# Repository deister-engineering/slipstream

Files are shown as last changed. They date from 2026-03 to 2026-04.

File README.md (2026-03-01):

# Slipstream

**This project is in beta. Please only attempt to build if you're an experienced builder and have a LOT of patience. Build instructions are not included.**

Slipstream is a high performance cross gantry/flying gantry 3D printer designed with scalability and speed in mind. It can be built as an open-air or fully enclosed printer, using a 2020 aluminum extrusion frame and MGN12H rails/carriages. The toolhead is based on the Annex K3, borrowing the MGN12H adaptation from @Etretti_376690 on Printables and modifying it to fit a Phaetus Rapido/Dragon hotend.

## Specifications
- Cross gantry cartesian kinematics
- Flying gantry (bed is static, gantry moves with Z axis)
- Quad-leveled gantry
- Enclosed or open air
- 2020 frame
- MGN12 rails/carriages
- Annex K3-based toolhead
- NEMA 17 motors for all axes of motion
- 9mm belts for XY motion, 6mm belts for Z
- 10:1 reduction pulley drive for Z axis

## Images

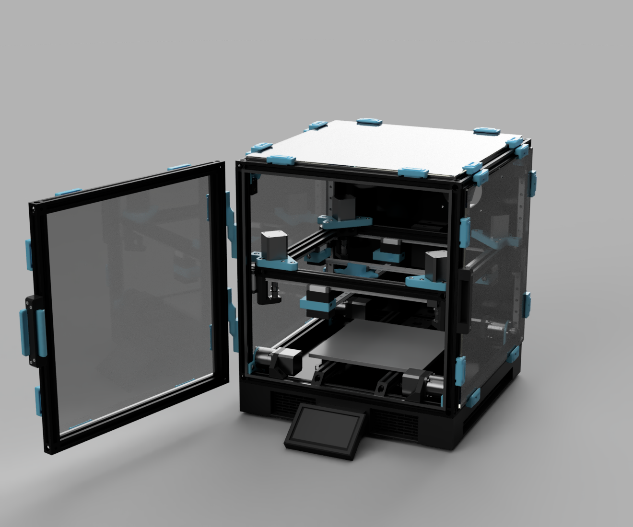
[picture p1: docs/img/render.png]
Image of Slipstream


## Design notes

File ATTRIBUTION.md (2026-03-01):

This project incorporates the following third-party works:

- MGN12H Rail + Carriage
  - by LiMo Bearing
  - Source: https://limobearing.com/3d-step-files
  - License can be found [here](https://limobearing.com/3d-step-files#:~:text=CAD%20File%20License%20Agreement)
  - Modifications: Rail chamfers removed for ease of positioning

- Fridge Door Lock Latch
  - by Inertia Bros
  - Source: https://github.com/Inertia-Bros/Inertia-Cube/tree/main/User-mods/2020%20Lock%20Latch%20-%20TheVoronModder
  - License: CC BY-NC-SA 4.0
  - Modifications: Removed logo, changed part colors, adjusted latch to clear thicker glass

- K3 MGN12 Toolhead
  - by @Etretti_376690
  - Source: https://www.printables.com/model/748199-k3-toolhead-carriage-mgn12
  - License: CC BY-NC 4.0
  - Modifications: Modified to fit Phaetus Rapido

- 5 inch DSI LCD
  - by Waveshare
  - Source: https://www.waveshare.com/wiki/5inch_DSI_LCD
  - License: No specific license, but was granted permission
  - No modifications

- Voron 2.4 Panel Locker
  - Copyright (c) 2024, v6cl
  - License: BSD 2-Clause
  - Source: https://github.com/v6cl/MyDIYthings/tree/main/3Dprinters/Utils/Panel_Locker
  - Modifications: spacing adjusted to support panel width, joints added to component for easier positioning + modeling. Changes are licensed under CC BY-NC-SA 4.0.
  - Panel Locker copyright notice: 
```
Voron 2.4 Panel Locker
BSD 2-Clause License

Copyright (c) 2024, v6cl

Redistribution and use in source and binary forms, with or without
modification, are permitted provided that the following conditions are met:

1. Redistributions of source code must retain the above copyright notice, this
   list of conditions and the following disclaimer.

2. Redistributions in binary form must reproduce the above copyright notice,
   this list of conditions and the following disclaimer in the documentation
   and/or other materials provided with the distribution.

THIS SOFTWARE IS PROVIDED BY THE COPYRIGHT HOLDERS AND CONTRIBUTORS "AS IS"
AND ANY EXPRESS OR IMPLIED WARRANTIES, INCLUDING, BUT NOT LIMITED TO, THE
IMPLIED WARRANTIES OF MERCHANTABILITY AND FITNESS FOR A PARTICULAR PURPOSE ARE
DISCLAIMED. IN NO EVENT SHALL THE COPYRIGHT HOLDER OR CONTRIBUTORS BE LIABLE
FOR ANY DIRECT, INDIRECT, INCIDENTAL, SPECIAL, EXEMPLARY, OR CONSEQUENTIAL
DAMAGES (INCLUDING, BUT NOT LIMITED TO, PROCUREMENT OF SUBSTITUTE GOODS OR
SERVICES; LOSS OF USE, DATA, OR PROFITS; OR BUSINESS INTERRUPTION) HOWEVER
CAUSED AND ON ANY THEORY OF LIABILITY, WHETHER IN CONTRACT, STRICT LIABILITY,
OR TORT (INCLUDING NEGLIGENCE OR OTHERWISE) ARISING IN ANY WAY OUT OF THE USE
OF THIS SOFTWARE, EVEN IF ADVISED OF THE POSSIBILITY OF SUCH DAMAGE.
```

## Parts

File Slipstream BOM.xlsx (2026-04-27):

Slipstream BOM - Beta | Fasteners are a rough minimum. Be prepared to purchase extras
 | Part Name | Number of items needed | Count of items per pack | Count to buy | Cost Each | Total Part Cost | Purchased? | Notes
Toolhead
 | GDSTIME 4020 Blower Fans (24V) (https://www.amazon.com/dp/B0DLKJ7WDJ) | 2 | 2 | 1 | $12.99 | $12.99 | FALSE
 | WINSINN 3010 Axial Fans (24V) (https://www.amazon.com/dp/B0757N6B8P) | 1 | 5 | 1 | $7.99 | $7.99 | FALSE
 | TZ-V6 2.0 (Choose any Dragon-compatible hotend) (https://www.amazon.com/Upgraded-Ceramic-Heatbreak-Hardened-Compatible/dp/B0CP64WYQW) | 1 | 1 | 1 | $28.99 | $28.99 | FALSE | Pretty sure this is a 2.0, so should be compatible with V6 nozzles
 | Fysetc CNC Sherpa Mini (https://www.amazon.com/FYSETC-Extruder-Temperature-Resistance-Compatible/dp/B0C3QGKQY6) | 1 | 1 | 1 | $85.66 | $85.66 | FALSE | There are more lightweight options
Glass
 | Acrylic Panels - SendCutSend Cart (https://cart.sendcutsend.com/7f6jah4ereyv) | 6 | 6 | 1 | $179.73 | $179.73 | FALSE | This cart is applicable if you're building a 220mm variant.
 | 5mm EVA foam tape (https://www.amazon.com/dp/B07L6LGMWC) | 8 | 4 | 2 | $7.19 | $14.38 | FALSE | Double this up - one strip on the frame side, one strip on the glass side. It will compress a bit
Frame
 | 2020 Extrusion - 400mm (https://www.amazon.com/dp/B0B2P434PD) | 16 | 10 | 2 | $36.99 | $73.98 | FALSE
 | 2020 Frame Block (https://www.amazon.com/dp/B0BG4TF813) | 16 | 8 | 2 | $16.89 | $33.78 | FALSE
 | 2020 90 Degree Frame Block 12x (https://www.amazon.com/dp/B0FRDJH8P2) | 4 | 12 | 1 | $18.39 | $18.39 | FALSE
Gantry
 | 2020 Extrusion - 350mm 4pcs (https://www.amazon.com/dp/B0B7DWDSYG) | 4 | 4 | 1 | $16.59 | $16.59 | FALSE
 | 2504 - 80mm shaft 48mm stepper (https://www.omc-stepperonline.com/nema-17-high-temp-stepper-motor-55ncm-77-93oz-in-80mm-5mm-d-cut-shaft-insulation-class-h-180c-17hs19-2504s-h-v5) | 4 | 1 | 4 | $15.00 | $60.00 | FALSE
 | MGN12H 350mm (https://www.amazon.com/CNCMANS-Miniature-Bearing-Printing-MGN12H-350mm/dp/B0BNQ99QWT) | 8 | 1 | 8 | $17.02 | $136.16 | FALSE
 | MGN12C 350mm (https://www.amazon.com/uxcell-Sliding-Carriage-Guideway-Engraving/dp/B0G5Y83MMT) | 2 | 1 | 2 | $19.99 | $39.98 | FALSE | These are for the cross rails. In the future, the outside rails of the gantry will likely move to MGN12C to cut down weight as well.
 | 625zz Bearing (https://www.amazon.com/uxcell-Groove-Bearings-Shielded-Bearing/dp/B0CJFRSK7D) | 8 | 25 | 1 | $7.79 | $7.79 | FALSE
 | GE5C Bearing (https://www.amazon.com/dp/B0CRNQYDFN) | 4 | 4 | 1 | $8.99 | $8.99 | FALSE
 | 9mm GT2 Timing Belt (10m) (https://www.amazon.com/dp/B0D7P815FL) | 1 | 1 | 1 | $25.99 | $25.99 | FALSE
 | 9mm GT2 Drive Pulley (https://www.amazon.com/dp/B0CNK9LKLV) | 4 | 10 | 1 | $12.98 | $12.98 | FALSE
 | 9mm GT2 Idler Pulley (https://www.amazon.com/dp/B0CNKBZFK8) | 4 | 10 | 1 | $13.98 | $13.98 | FALSE
 | 5mm to 5mm Shaft Coupling (https://www.amazon.com/dp/B0D4575J9B) | 4 | 10 | 1 | $8.49 | $8.49 | FALSE | Needed if going with steppers that don't have 80mm shafts. Recommend ~23mm shaft length from mounting face of stepper (OMC 17HS19-2004S1 are a good fit)
 | m5x8mmx0.5mm shims 100pk (https://www.amazon.com/dp/B0CF9H1R76) | 8 | 100 | 1 | $7.99 | $7.99 | FALSE
 | m5x8mmx1mm shims 50pk (https://www.fabreeko.com/products/m5-precision-brass-shims-m5x7x0-5?variant=45416233468159) | 8 | 100 | 1 | $6.99 | $6.99 | FALSE
Electronics
 | Meanwell LRS-350-48 (https://www.amazon.com/LRS-350-48-Switching-180-264VAC-Industrial-Efficient/dp/B0DJW8CMNJ) | 1 | 1 | 1 | $31.26 | $31.26 | FALSE
 | Meanwell LRS-350-24 (https://www.amazon.com/MEAN-WELL-LRS-350-24-350-4W-Switchable/dp/B013ETVO12) | 1 | 1 | 1 | $28.54 | $28.54 | FALSE
 | BTT Kraken (https://www.amazon.com/BIGTREETECH-Control-Onboard-8%C3%97TMC2160-Drivers/dp/B0F7RQY6Z4) | 1 | 1 | 1 | $129.99 | $129.99 | FALSE
 | Raspberry Pi 3B+ or newer (https://www.amazon.com/ELEMENT-Element14-Raspberry-Pi-Motherboard/dp/B07BDR5PDW) | 1 | 1 | 1 | $50.00 | $50.00 | FALSE
 | Fused IEC inlet (https://www.amazon.com/Qjaiune-IEC320-Socket-Rocker-Switch/dp/B09QFK6W2C) | 1 | 6 | 1 | $8.99 | $8.99 | FALSE
 | Cartographer V4 (https://cartographer3d.com/products/cartographer-v4-aio-standard) | 1 | 1 | 1 | $39.99 | $39.99 | FALSE
 | CAN wire (https://cartographer3d.com/products/microfit-3-0-can-cable-for-ebb36) | 1 | 1 | 1 | $15.00 | $15.00 | FALSE
Z axis
 | Creality 42-34 or comparable (14-18mm shaft length) (https://www.amazon.com/Creality-Official-42-34-3D-Compatible/dp/B09LQKWF7F) | 4 | 1 | 4 | $12.99 | $51.96 | FALSE
 | Stepperonline MG17-G10 Gearbox (https://www.omc-stepperonline.com/mg-series-planetary-gearbox-gear-ratio-10-1-backlash-30-arc-min-for-nema-17-stepper-motor-mg17-g10) | 4 | 1 | 4 | $15.60 | $62.40 | FALSE
 | GT2 20 tooth pulley/8mm bore/6mm belt (5 pack) (https://www.amazon.com/dp/B077GMKW1C) | 4 | 5 | 1 | $6.99 | $6.99 | FALSE
 | 15x15mm Cable Chain (https://www.amazon.com/dp/B07QYM88MQ) | 1 | 1 | 1 | $13.99 | $13.99 | FALSE
Bed
 | 235mm heated bed (any 4-point bed will do) (https://www.amazon.com/Aluminum-Heatbed-235%C3%97235x3mm-Ender-3-Printers/dp/B08DRJM9S4) | 1 | 1 | 1 | $22.99 | $22.99 | FALSE | Nicer option here. If you choose this, upgrade the 24v PSU to an LRS-350-24 or plan on getting an AC heater + a relay (https://www.amazon.com/dp/B0CMCDBJJF)
 | 235mm PEI build plate (https://www.amazon.com/235x235mm-Texture-Magnetic-Flexible-Creality/dp/B0CRDS6PRR) | 1 | 1 | 1 | $12.99 | $12.99 | FALSE
General
 | M2 heat inserts (https://www.amazon.com/dp/B0CTCQ6MHK) | 10 | 100 | 1 | $7.59 | $7.59 | FALSE | Only substitute exact dimensions. Count needed is approximate
 | M3 heat inserts 100ct (https://www.amazon.com/dp/B08TRK72TR) | 50 | 100 | 1 | $11.99 | $11.99 | FALSE | Only substitute exact dimensions. Count needed is approximate
 | M5 heat inserts 100ct (https://www.amazon.com/dp/B0F8HMZHTK) | 20 | 100 | 1 | $7.99 | $7.99 | FALSE | Only substitute exact dimensions. Count needed is approximate
 | Rubber Feet (https://www.amazon.com/Reliable-Hardware-Company-RH-1606-8-Amplifier/dp/B00JJ191Z6) | 4 | 8 | 1 | $9.99 | $9.99 | FALSE
 | Cable Chain (https://www.amazon.com/dp/B07QLGWQ1L) | 1 | 1 | 1 | $14.49 | $14.49 | FALSE
Fasteners | There are likely some fasteners missed in this list.
 | Hexagon Socket Button Head Screw ISO 7380-1 - M3 x 10 Steel 4.6 Plain |  | 16
 | Hexagon Socket Button Head Screw ISO 7380-1 - M3 x 16 Steel 4.6 Plain |  | 4
 | Hexagon Socket Button Head Screw ISO 7380-1 - M3 x 30 Steel 4.6 Plain |  | 8
 | Hexagon Socket Button Head Screw ISO 7380-1 - M3 x 55 Steel 4.6 Plain |  | 8
 | Hexagon Socket Button Head Screw ISO 7380-1 - M3 x 6 Steel 4.6 Plain |  | 8
 | Hexagon Socket Button Head Screw ISO 7380-1 - M3 x 8 Steel 4.6 Plain |  | 16
 | Hexagon Socket Button Head Screw ISO 7380-1 - M5 x 10 Steel 4.6 Plain |  | 12
 | Hexagon Socket Button Head Screw ISO 7380-1 - M5 x 12 Steel 4.6 Plain |  | 8
 | Hexagon Socket Button Head Screw ISO 7380-1 - M5 x 16 Steel 4.6 Plain |  | 56
 | Hexagon Socket Button Head Screw ISO 7380-1 - M5 x 20 Steel 4.6 Plain |  | 8
 | Hexagon Socket Button Head Screw ISO 7380-1 - M5 x 25 Steel 4.6 Plain |  | 2
 | Hexagon Socket Button Head Screw ISO 7380-1 - M5 x 30 Steel 4.6 Plain |  | 3
 | Hexagon Socket Button Head Screw ISO 7380-1 - M5 x 60 Steel 4.6 Plain |  | 4
 | Hexagon Socket Button Head Screw ISO 7380-1 - M5 x 75 Steel 4.6 Plain |  | 5
 | Hexagon Socket Button Head Screw ISO 7380-1 - M5 x 8 Steel 4.6 Plain |  | 28
 | Hexagon Socket Button Head Screw ISO 7380-1 - M5 x 90 Steel 4.6 Plain |  | 5
 | Hexagon Socket Head Cap Screw DIN 912 - M3 x 0.5 x 12 Steel 4.6 Plain |  | 6
 | Hexagon Socket Head Cap Screw DIN 912 - M3 x 0.5 x 16 Steel 4.6 Plain |  | 42
 | Hexagon Socket Head Cap Screw DIN 912 - M3 x 0.5 x 20 Steel 4.6 Plain |  | 24
 | Hexagon Socket Head Cap Screw DIN 912 - M3 x 0.5 x 25 Steel 4.6 Plain |  | 16
 | Hexagon Socket Head Cap Screw DIN 912 - M3 x 0.5 x 8 Steel 4.6 Plain |  | 108
 | Hexagon Socket Head Cap Screw DIN 912 - M4 x 0.7 x 12 Steel 4.6 Plain |  | 6
 | Hexagon Socket Head Cap Screw DIN 912 - M5 x 0.8 x 10 Steel 4.6 Plain |  | 2
 | M3x30 Socket Cap Screw |  | 4
 | M2 Heat Insert |  | 9
 | M2.5 Heat Insert |  | 5
 | M3 hexagon socket screw head |  | 32
 | M3 Heat Insert |  | 41
 | M3x5x4mm Heated Insert |  | 3
 | M5 Heat Insert |  | 18
 |  |  |  |  | TOTAL | $1314.47
 |  |  |  |  | TOTAL REMAINING | $1314.47

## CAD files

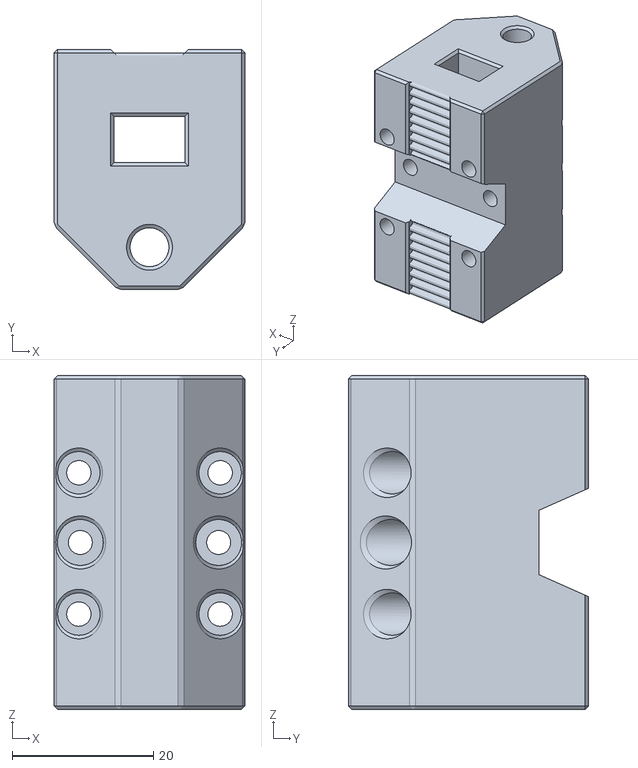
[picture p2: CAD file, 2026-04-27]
stl/z_axis/carriage/Main_Z_Carriage_Body(x4).stl
27.0 x 34.0 x 47.3

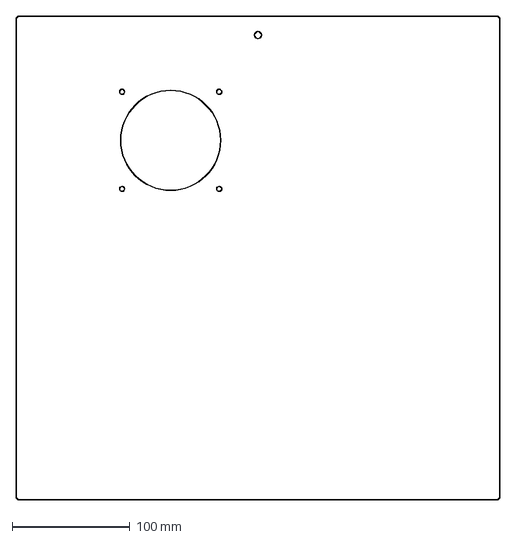
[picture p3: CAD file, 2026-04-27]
dxf/glass/Rear_Glass_With_Exhaust_Filament_Inlet.dxf
411.5 x 411.5 mm

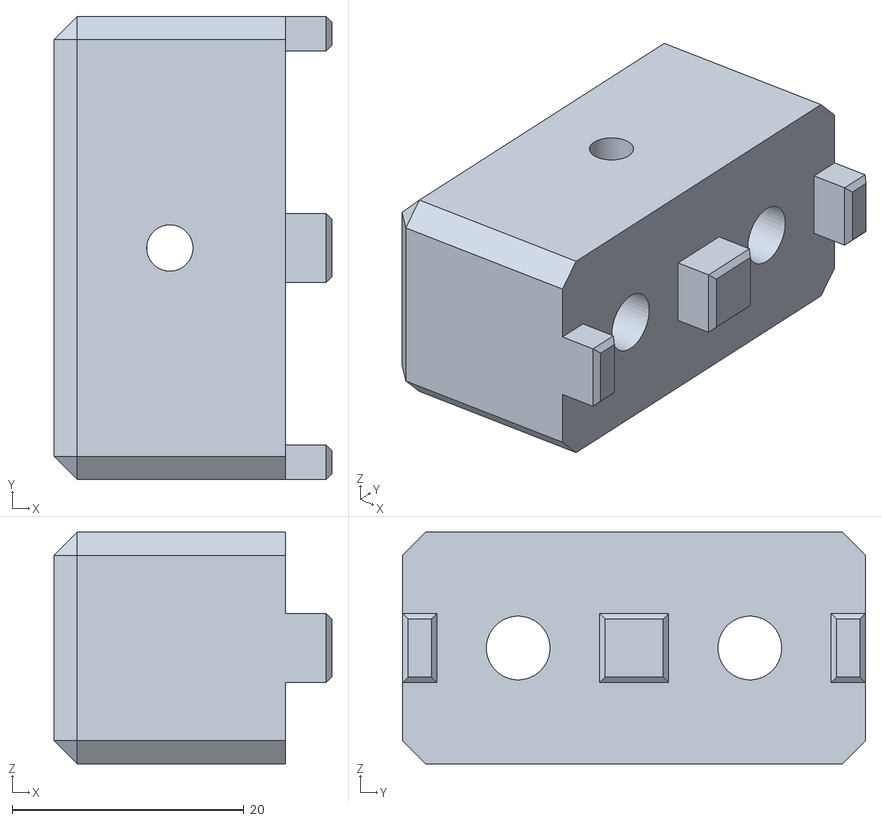
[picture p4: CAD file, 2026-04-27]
stl/bed/bed_mount(x4).stl
24.0 x 40.0 x 20.0

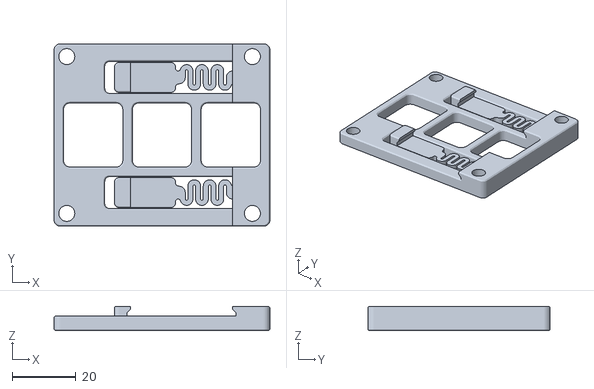
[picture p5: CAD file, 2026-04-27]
stl/electronics/Kraken_DIN_Mount(x2).stl
67.5 x 57.0 x 7.60

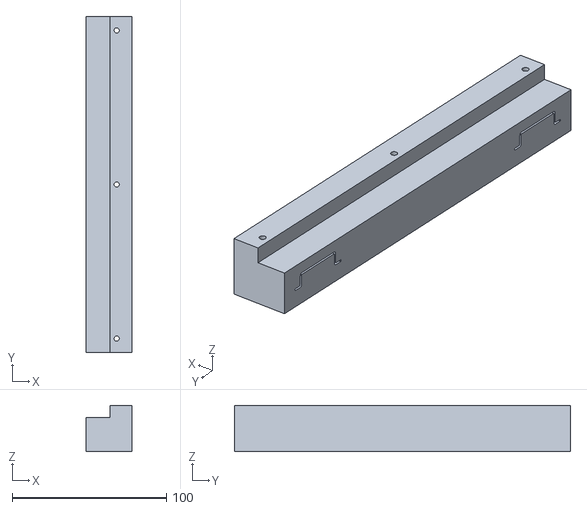
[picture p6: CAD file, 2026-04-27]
stl/feet_and_sideskirts/35x7.5_400mm_DIN_Sideskirt(x2).stl
30.0 x 218.0 x 30.0

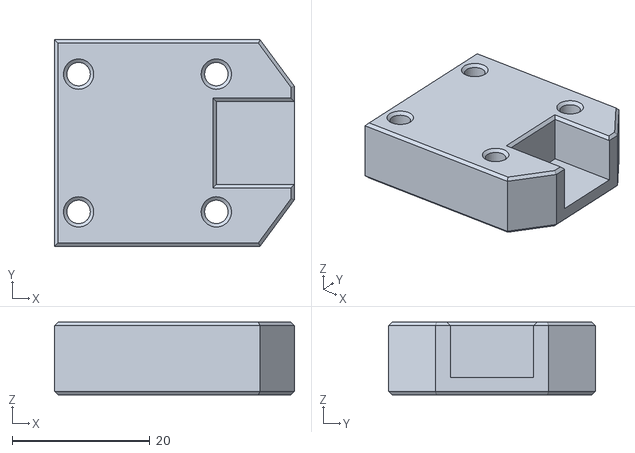
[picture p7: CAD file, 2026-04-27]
stl/gantry/carriage/Carriage_Rail_Retainer(x4).stl
34.9 x 30.0 x 10.5

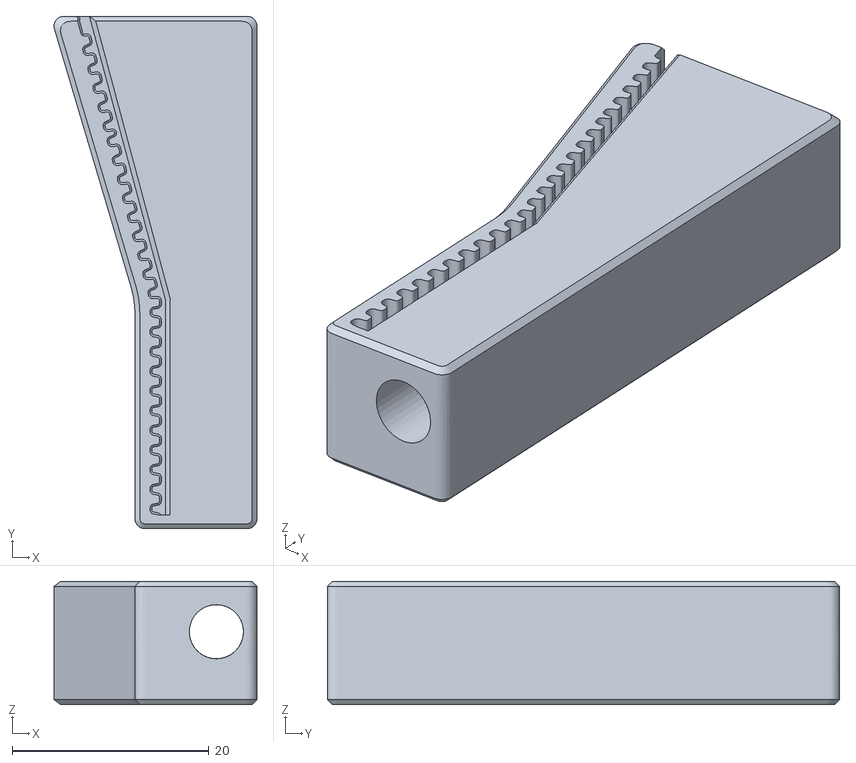
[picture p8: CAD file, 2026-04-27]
stl/gantry/carriage/tensioner/[a]Tensioner_Block(x2).stl
20.6 x 52.1 x 12.5

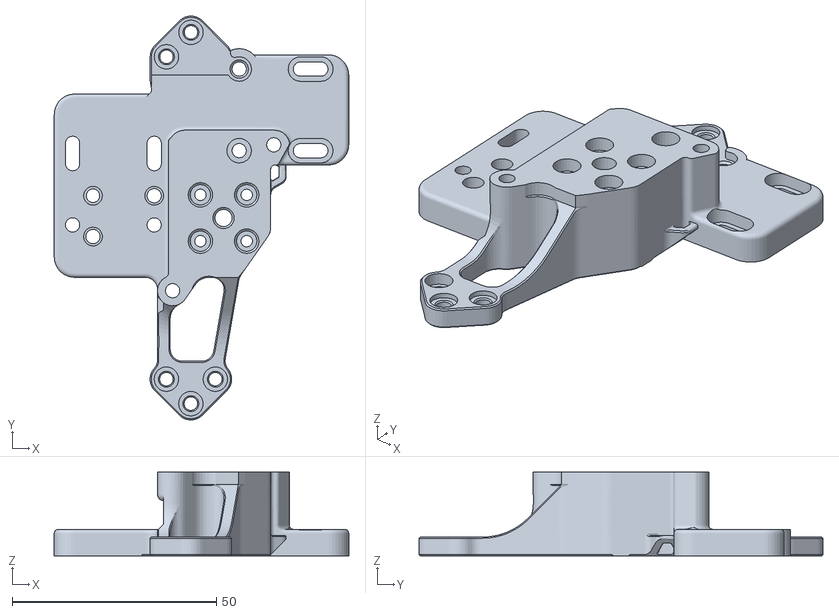
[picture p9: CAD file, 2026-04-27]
stl/gantry/carriage/toolhead/[a]toolhead_body.stl
72.2 x 99.0 x 20.5

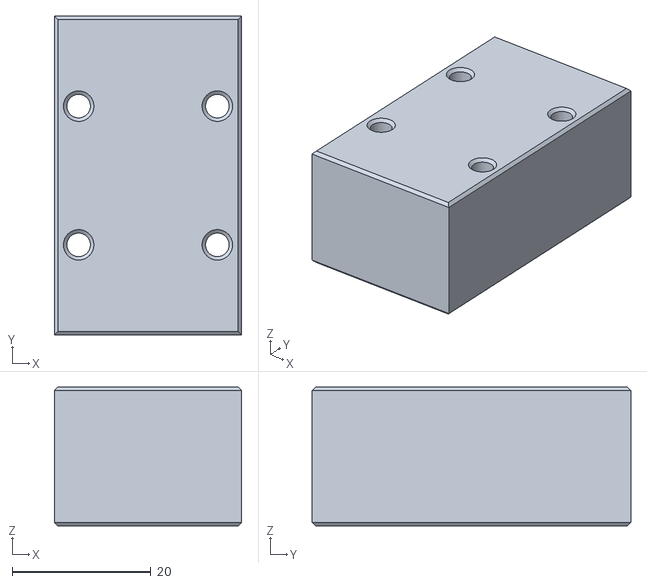
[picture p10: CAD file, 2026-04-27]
stl/gantry/carriage/y_carriage/Carriage_Spacer.stl
27.0 x 46.0 x 20.0

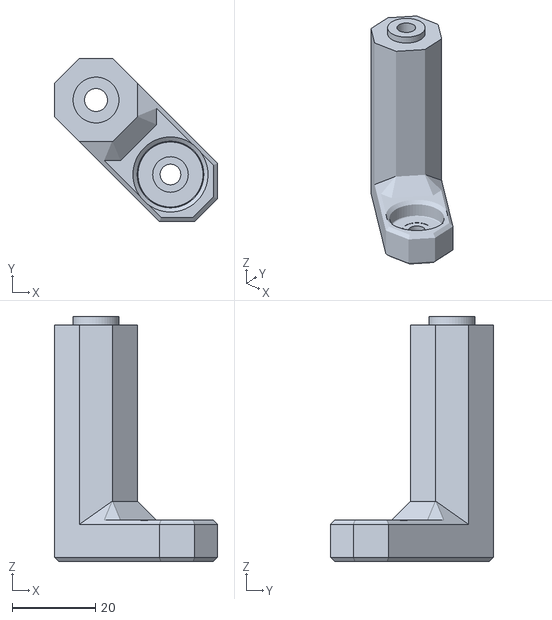
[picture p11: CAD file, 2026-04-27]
stl/gantry/Lower_Bearing_Retainer(x4).stl
39.2 x 39.2 x 58.8

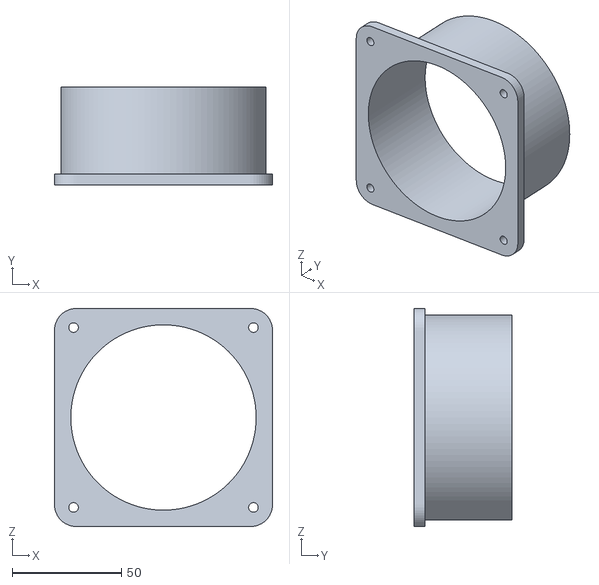
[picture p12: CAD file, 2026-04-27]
stl/glass_tabs/92mm_4in_Fan_Duct.stl
100.0 x 45.0 x 100.0

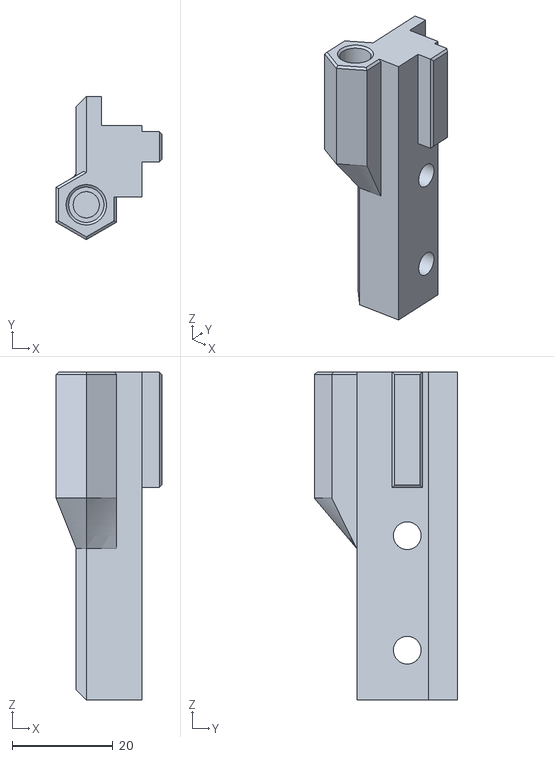
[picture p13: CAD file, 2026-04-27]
stl/i3_lock_latch/[a]Glass_Hinge_Tab(x2).stl
21.0 x 28.4 x 65.0

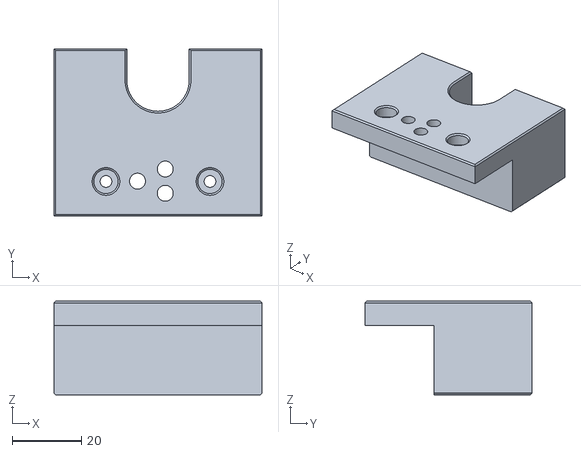
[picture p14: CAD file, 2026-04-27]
stl/Strain_Relief.stl
60.0 x 48.2 x 27.0

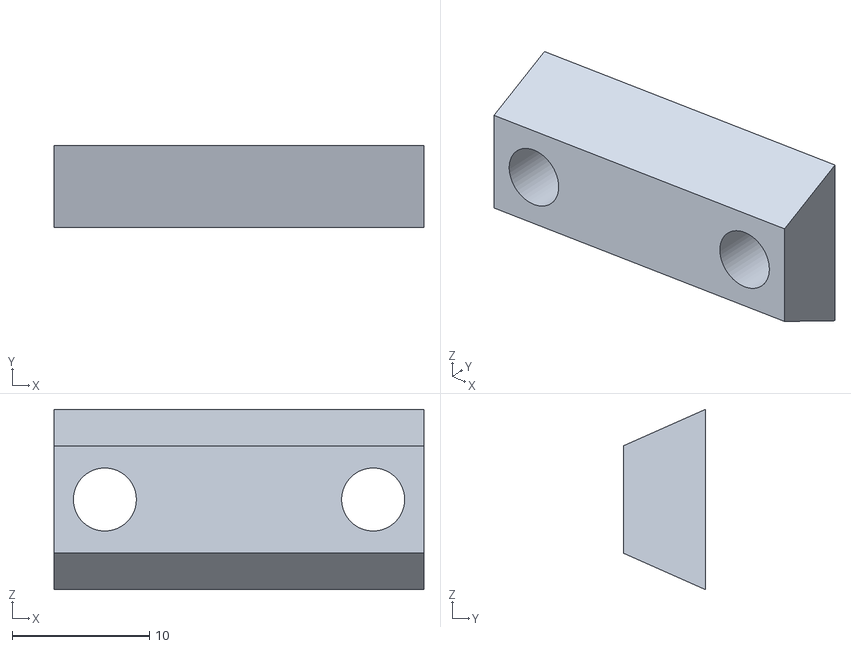
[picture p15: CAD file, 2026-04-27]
stl/z_axis/carriage/Z_Belt_Retainer(x4).stl
27.0 x 6.00 x 13.2

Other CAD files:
stl/z_axis/lower_drive/[a]Stepper_Planetary_Spacer_Bracket(Mirror)(x2).stl
stl/z_axis/tensioner/Knob(x4).stl
stl/z_axis/Vertical_Rail_Stop_Block.stl
dxf/glass/Underside_Glass.dxf
dxf/glass/Side_And_Top_Glass.dxf
dxf/glass/Side_Glass_With_Filament_Hole.dxf
stl/Strain_Relief_Cap.stl
stl/electronics/Kraken_Plate.stl
stl/electronics/LRS-150_Mount.stl
stl/electronics/LRS-350_DIN_Mount(x2).stl
stl/electronics/LRS-350_Mount_Long.stl
stl/feet_and_sideskirts/Display_Mount.stl
stl/feet_and_sideskirts/Foot(x4).stl
stl/feet_and_sideskirts/Front_Sideskirt(x2).stl
stl/feet_and_sideskirts/IEC_Inlet_Housing.stl
stl/feet_and_sideskirts/Rear_Sideskirt.stl
stl/feet_and_sideskirts/Sideskirt_DIN_Cover(x2).stl
stl/feet_and_sideskirts/Waveshare_5in_DSI_Housing.stl
stl/feet_and_sideskirts/Waveshare_5in_DSI_Lid.stl
stl/gantry/Cable_Retainer_Housing.stl
stl/gantry/Cable_Retainer_Lid.stl
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

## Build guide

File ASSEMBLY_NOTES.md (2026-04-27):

# Assembly Notes

#### This document is meant to be for use by beta testers and not a long-term solution. It contains information and "gotchas" that we've run into during assembly. Eventually, this document will inform as we create an assembly manual.

### Recommended Order
There isn't really a _right_ order, but there are definitely wrong orders to assemble the printer in.
We'd recommend building the frame (SQUARE IT BEFORE CONTINUING FURTHER), sideskirts, Z drive assembly, bed assembly, then the electronics.

Gantry should be assembled and tensioned (120hz at 150mm) outside of the printer, then can be moved into the printer. Ensure all 4 corners of the Z axis are the same tension (recommended this is tensioned to ~140hz at 150mm) around the same height (this can be done with a ruler). Moving the gantry into the printer can be finnicky and is best done with an extra pair of hands.

It's recommended to add the EVA foam tape, panels, and locking clips after the gantry is in. 

### Z Drive Assembly
The rails are set to index against the bottom of the Z axis belt tensioners. It's recommended to install the tensioners, then the Z rail stop blocks, then the rails, then the lower Z drive assembly. For the lower Z drive assembly, PAY CLOSE ATTENTION to which parts are mirrored and which parts are not. They are _not_ interchangeable as the motors are not mounted a direct 45 degrees off of the frame. Failure to follow this will result in the drive pulley being out of alignment with the top pulley, causing the belt to rub against the Z carriage.

### XY Pulley Stacks
The bearing/washer/pulley stack order should be as follows, starting from the side closest to the motor and ending on the bottom of the stack.

Top-driven:
- 625zz bearing
- 0.5mm washer
- Drive pulley (grub screws below)
- 0.5mm washer
- 1mm washer
- Idler pulley
- 1mm washer
- 625zz bearing

Bottom-driven:
- 625zz bearing
- 0.5mm washer
- Idler pulley
- 0.5mm washer
- 1mm washer
- Drive pulley (grub screws above)
- 1mm washer
- 625zz bearing

### XY Tensioners
The belts are routed in a similar manner to how Annex Engineering tensions the XY belts on the K3. Ensure the belt loop that the M3 screw goes through has at least 10 teeth on each side meshing with itself (so, fold over ~1in of belt). 

On the side that interfaces with the moving tensioner block, ensure that ALL teeth mesh. The more contact, the better, so that the belt doesn't slip out of the tensioner block.

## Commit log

2026-01-04 feat: bed mounted properly, base color printed parts all consistently colored, alignment fixtures added to all tabs
2026-01-09 feat: rough STLs, switch to direct modeling, add hardware
    [Cable_Retainer_Flying_Cross_Gantry v91_Body1.stl, Cable_Retainer_Flying_Cross_Gantry v91_Body2.stl, Motor_Mount(Mirror).stl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]
2026-01-09 feat: Z axis reworked, full 220mm volume
2026-01-10 feat: added screen housing for Waveshare 5" DSI, z axis spherical bearing retainers complete
2026-01-10 feat: added endstop mount
2026-01-18 feat: XY bearing retainer redesign, filament hole added, DIN rails better spaced
    [35x7.5_400mm_din_sideskirt(2x).stl, Cable_Retainer_Flying_Cross_Gantry v91_Body1.stl, Cable_Retainer_Flying_Cross_Gantry v91_Body2.stl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]
2026-01-28 feat: alpha revisions, z axis drive redesign, XY bearing retainer redesign, electronics complete
    [Cable_Retainer_Housing.stl, Cable_Retainer_Lid.stl, Cable_Retainer_Slipstream v118_Housing.stl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]
2026-03-01 feat: beta release
    [35x7.5_400mm_din_sideskirt(2x).stl, 8mm_Panel_Locker.stl, 92mm_4in_Fan_Duct.stl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]
2026-03-01 hotfix: add 625zz bearings to BOM
    [Slipstream BOM.xlsx]
2026-04-27 fix: clean up BOM per feedback
    [2020 Front Latch Lower.stl, 2020 Front Latch Upper.stl, 2020 Mount Lower.stl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]
